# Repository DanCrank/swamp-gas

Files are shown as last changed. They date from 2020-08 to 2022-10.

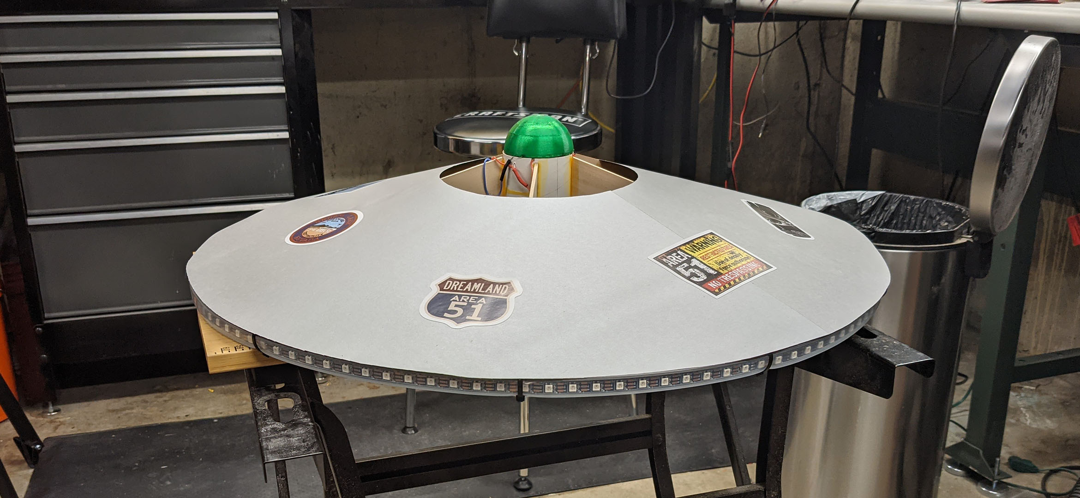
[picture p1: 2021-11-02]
swamp-gas-in-workshop.jpg

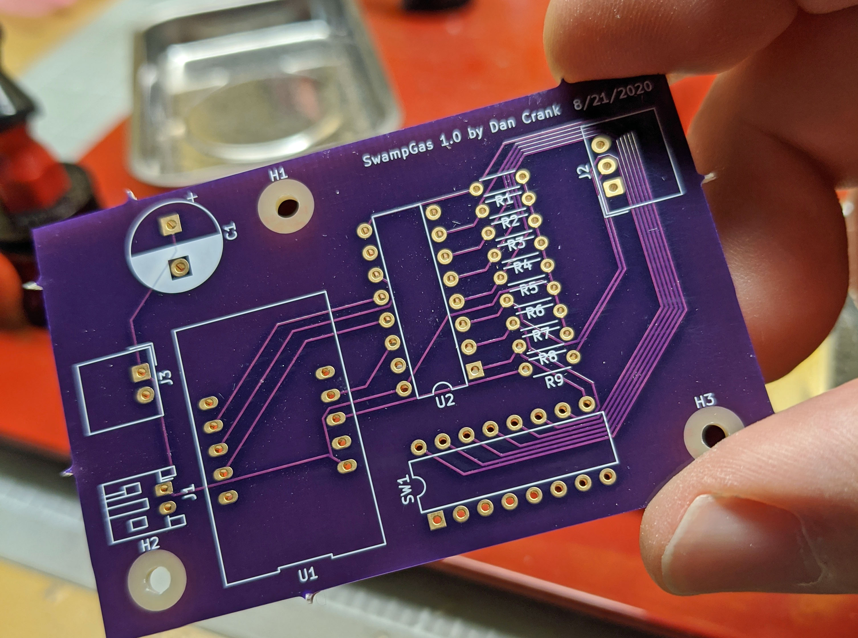
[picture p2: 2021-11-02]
lighting-controller/board/images/pcb-1.jpg

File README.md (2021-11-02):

# swamp-gas
Design for an illuminated saucer rocket

```
/3d-objects              STL files for 3D-printed parts
                         F3D and STEP files for complete rocket
/lighting-controller
  /arduino/swamp-gas     Arduino code for the lighting program
  /board                 design files for carrier PCB
    /images              images of the layout and manufactured board
```

Parts list:
- 29mm motor tube, 100mm long
- 2.6" body tube, 100mm long
- 29mm motor retainer
- 5 fins cut from 1/8" basswood, per template
- 2-meter Adafruit NeoPixel strand, 60 pixels/meter
- Adafruit Trinket M0
- Custom carrier PCB
- 4 green LEDs mounted in top of body tube to illuminate the dome
    (wired in parallel, with a current limiting resistor if needed)
- 400mAh LiPo battery (zip tied to one of the fins)
- 26 ga stranded wire
- 2-pin JST connectors for battery
- 3-pin Molex connectors for connection to NeoPixel strand
- 2-pin Molex connectors for connection to LEDs in dome
- Power switch (optional)

LED wiring is left as an exercise for the reader and will depend on
the specific LEDs and battery you use.

In the first flight, the saucer flipped nose-down at apogee and fell
in a stable nose-down orientation, so no parachute should be needed.
The nose cone can be permanently mounted in the motor tube with CA.
Make sure the ejection sharge is removed from the motor before flight.

First flight was at the St. Louis Rocketry Association Spooktacular
Night Launch on October 30, 2021.

https://youtu.be/KtkhaTuiWWw

Hardware and software designs in this repository are distributed under
GNU GPLv3. (See COPYING for full license.)

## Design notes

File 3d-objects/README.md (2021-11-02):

The nose cone was printed in translucent green PETG; the other parts
were printed in PLA.

The rocket was designed in Autodesk Fusion 360 (hobbyist version);
the full design of the rocket is provided in Fusion 360 format (.f3d)
and as a .step file.

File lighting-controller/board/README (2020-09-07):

Board designed with KiCad 5.1.6. https://www.kicad-pcb.org

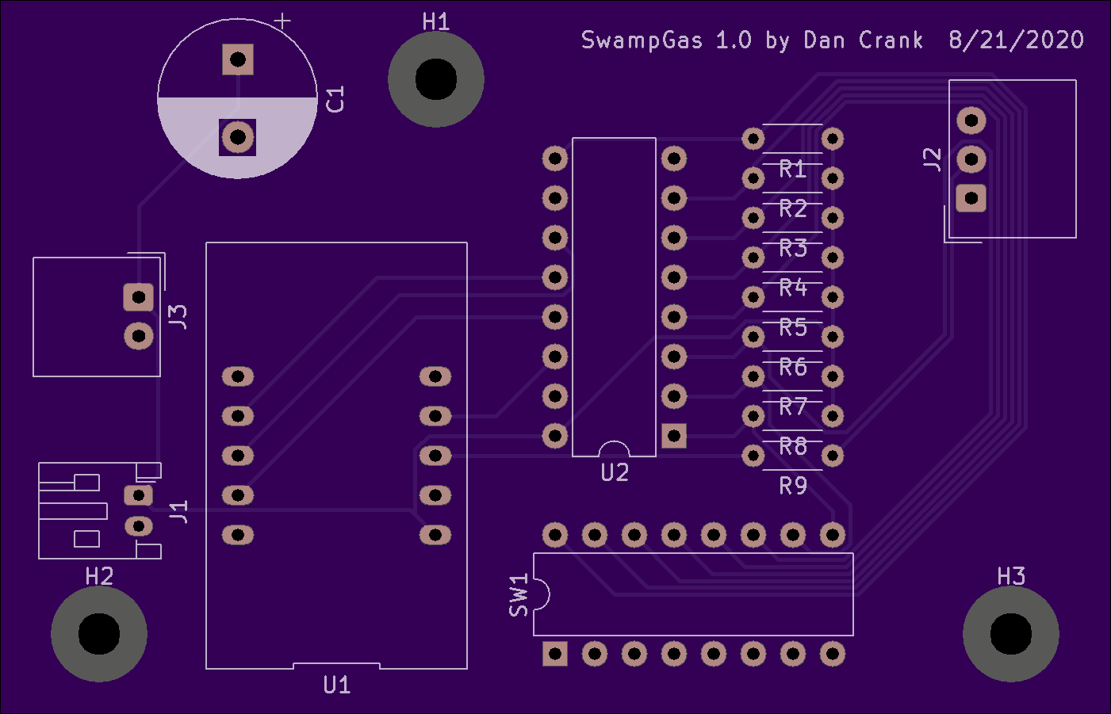
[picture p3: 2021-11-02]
lighting-controller/board/images/fab-1.0.png

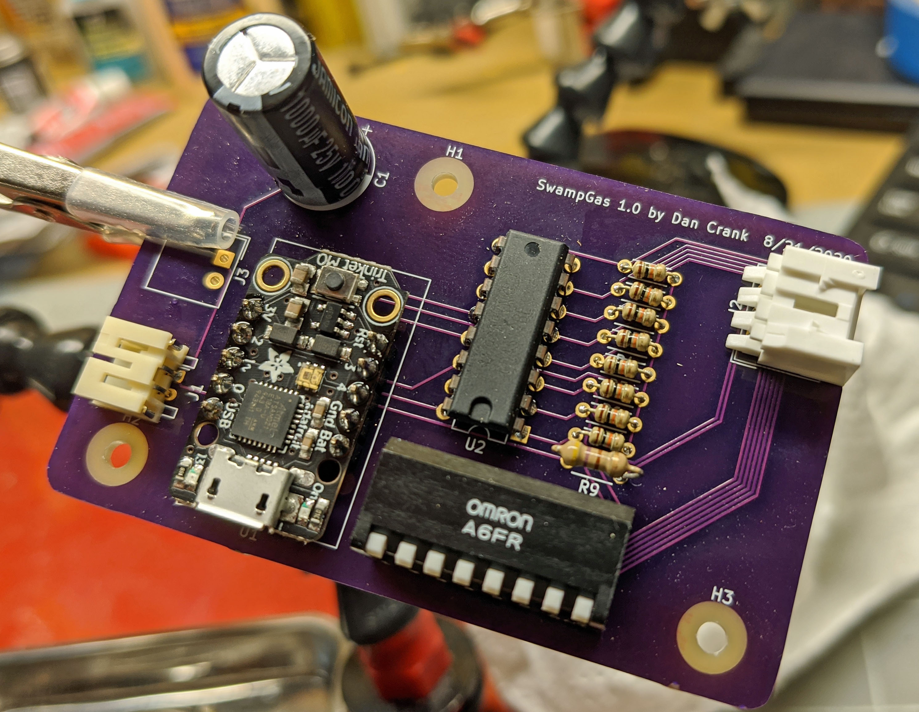
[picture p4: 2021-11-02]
lighting-controller/board/images/pcb-2.jpg

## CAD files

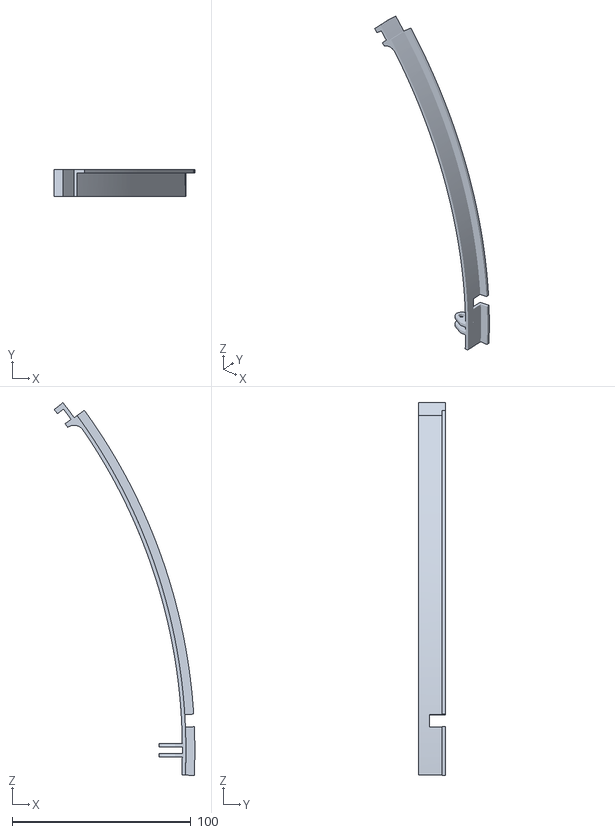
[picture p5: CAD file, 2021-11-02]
3d-objects/ring-b-with-slot.stl
78.6 x 15.0 x 208.5

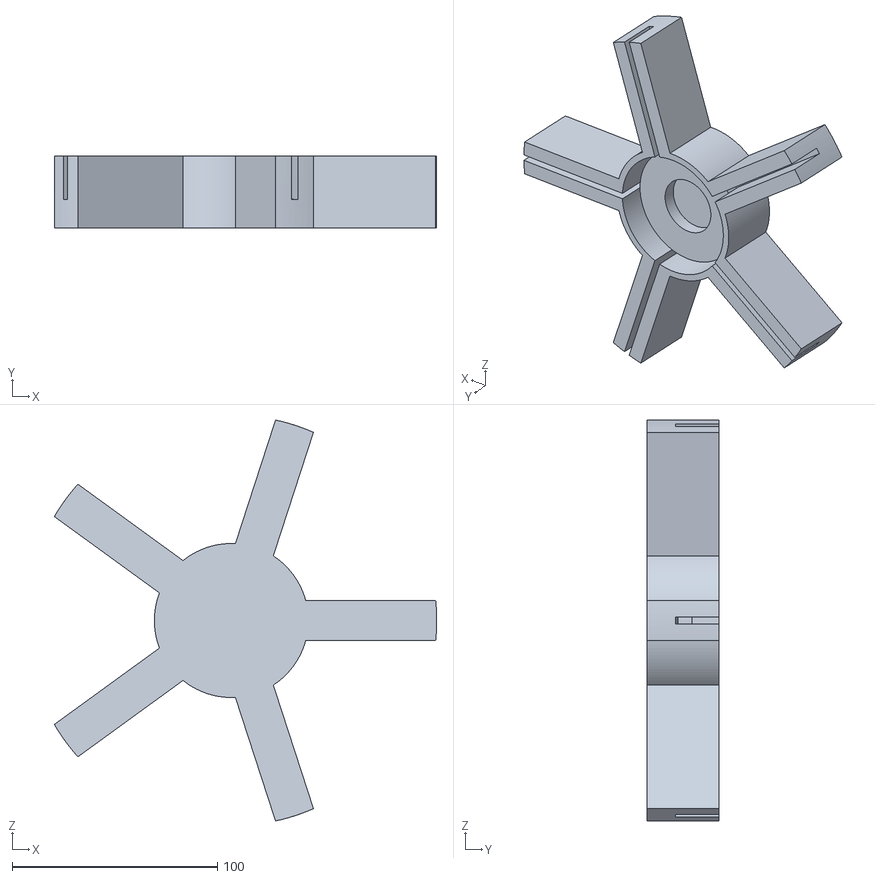
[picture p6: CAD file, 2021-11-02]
3d-objects/FinJig.stl
186.2 x 35.0 x 195.3

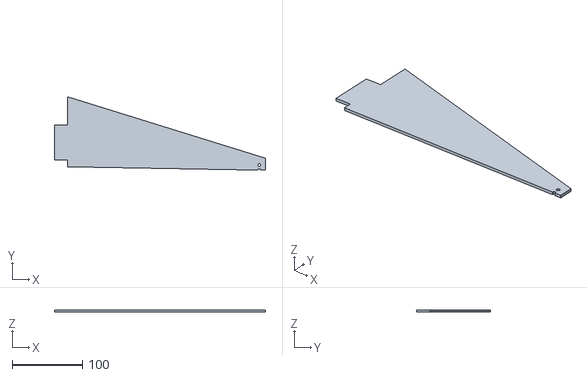
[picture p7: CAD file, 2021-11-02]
3d-objects/fin-template.stl
301.2 x 104.9 x 3.11

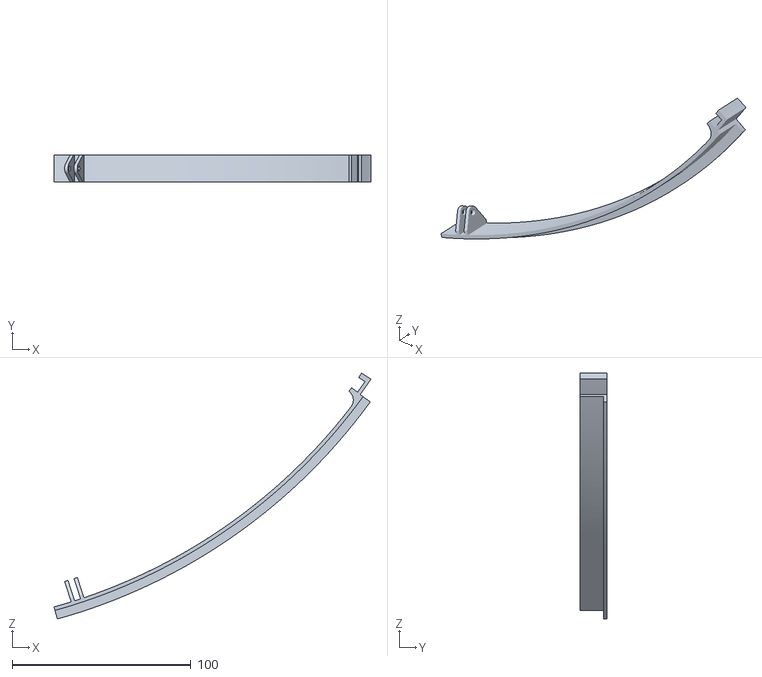
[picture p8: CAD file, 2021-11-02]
3d-objects/ring-b.stl
177.4 x 15.0 x 137.7

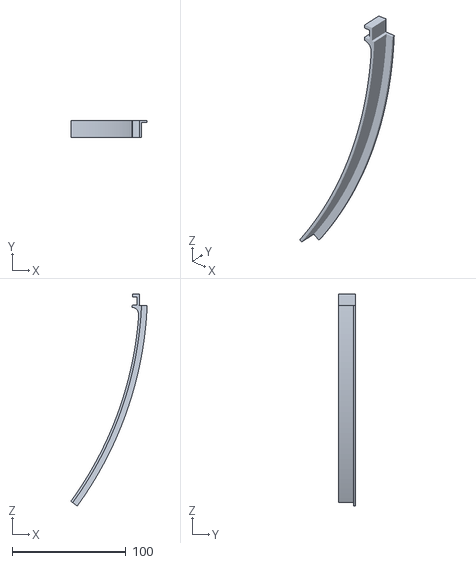
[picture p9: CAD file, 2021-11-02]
3d-objects/ring-a.stl
67.1 x 15.0 x 186.2

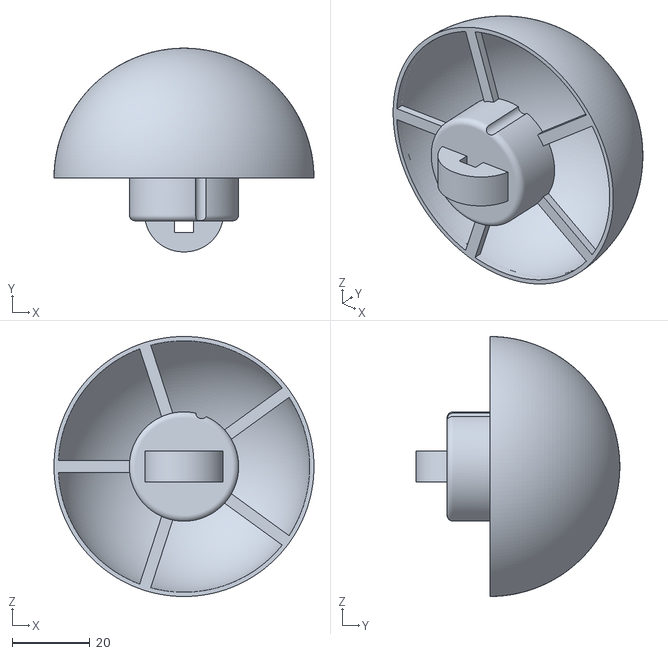
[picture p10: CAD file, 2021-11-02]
3d-objects/nose-cone-2.stl
67.1 x 52.5 x 67.1

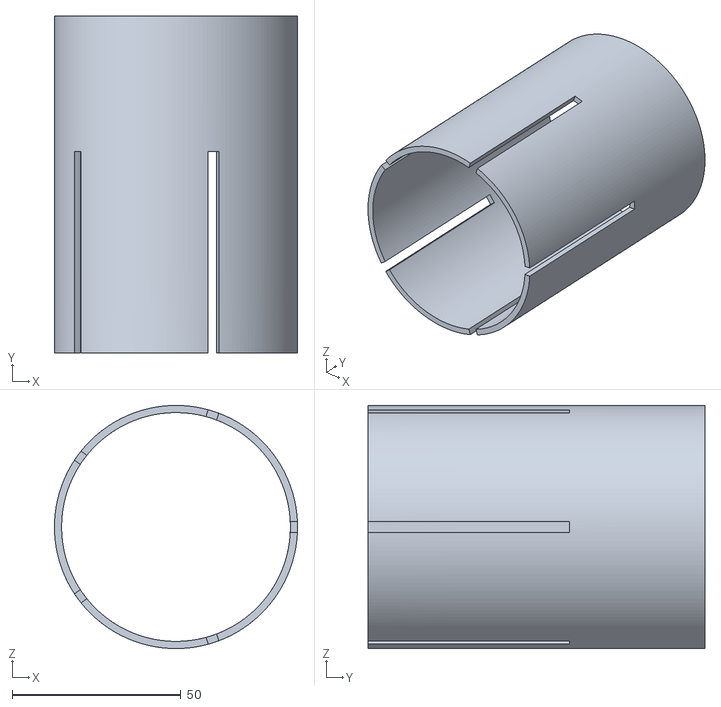
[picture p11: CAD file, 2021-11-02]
3d-objects/SlottingJig.stl
72.0 x 99.8 x 72.0

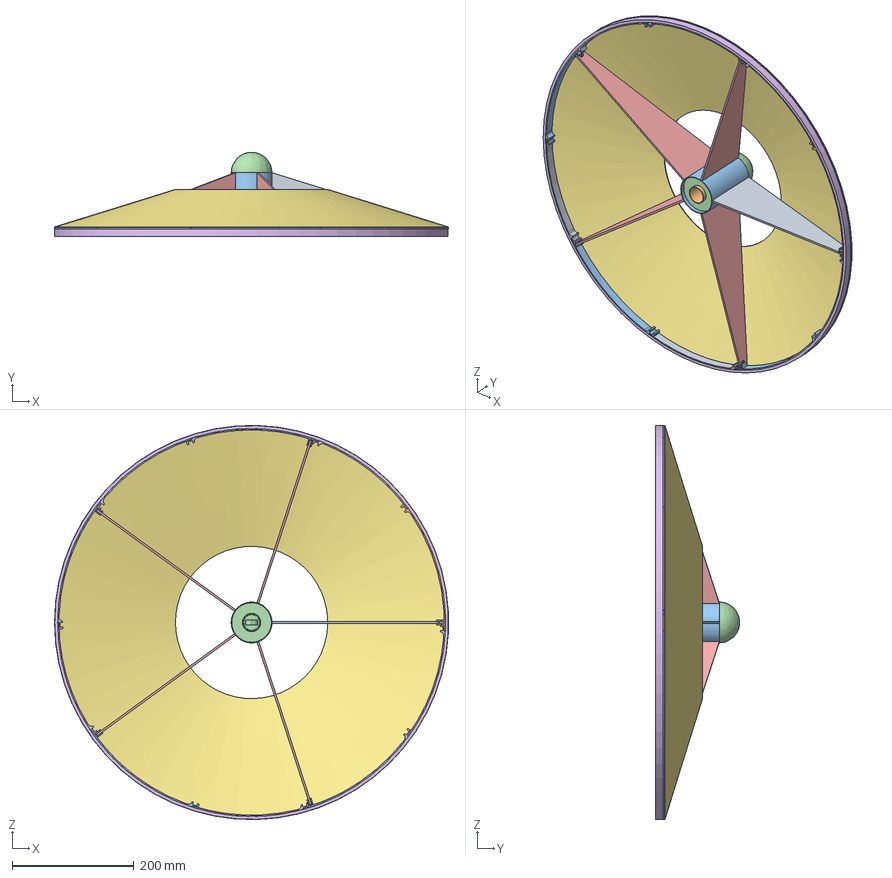
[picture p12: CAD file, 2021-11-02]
3d-objects/SwampGas.step
646.9 x 138.5 x 647.0 mm

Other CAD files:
3d-objects/SwampGas.f3d

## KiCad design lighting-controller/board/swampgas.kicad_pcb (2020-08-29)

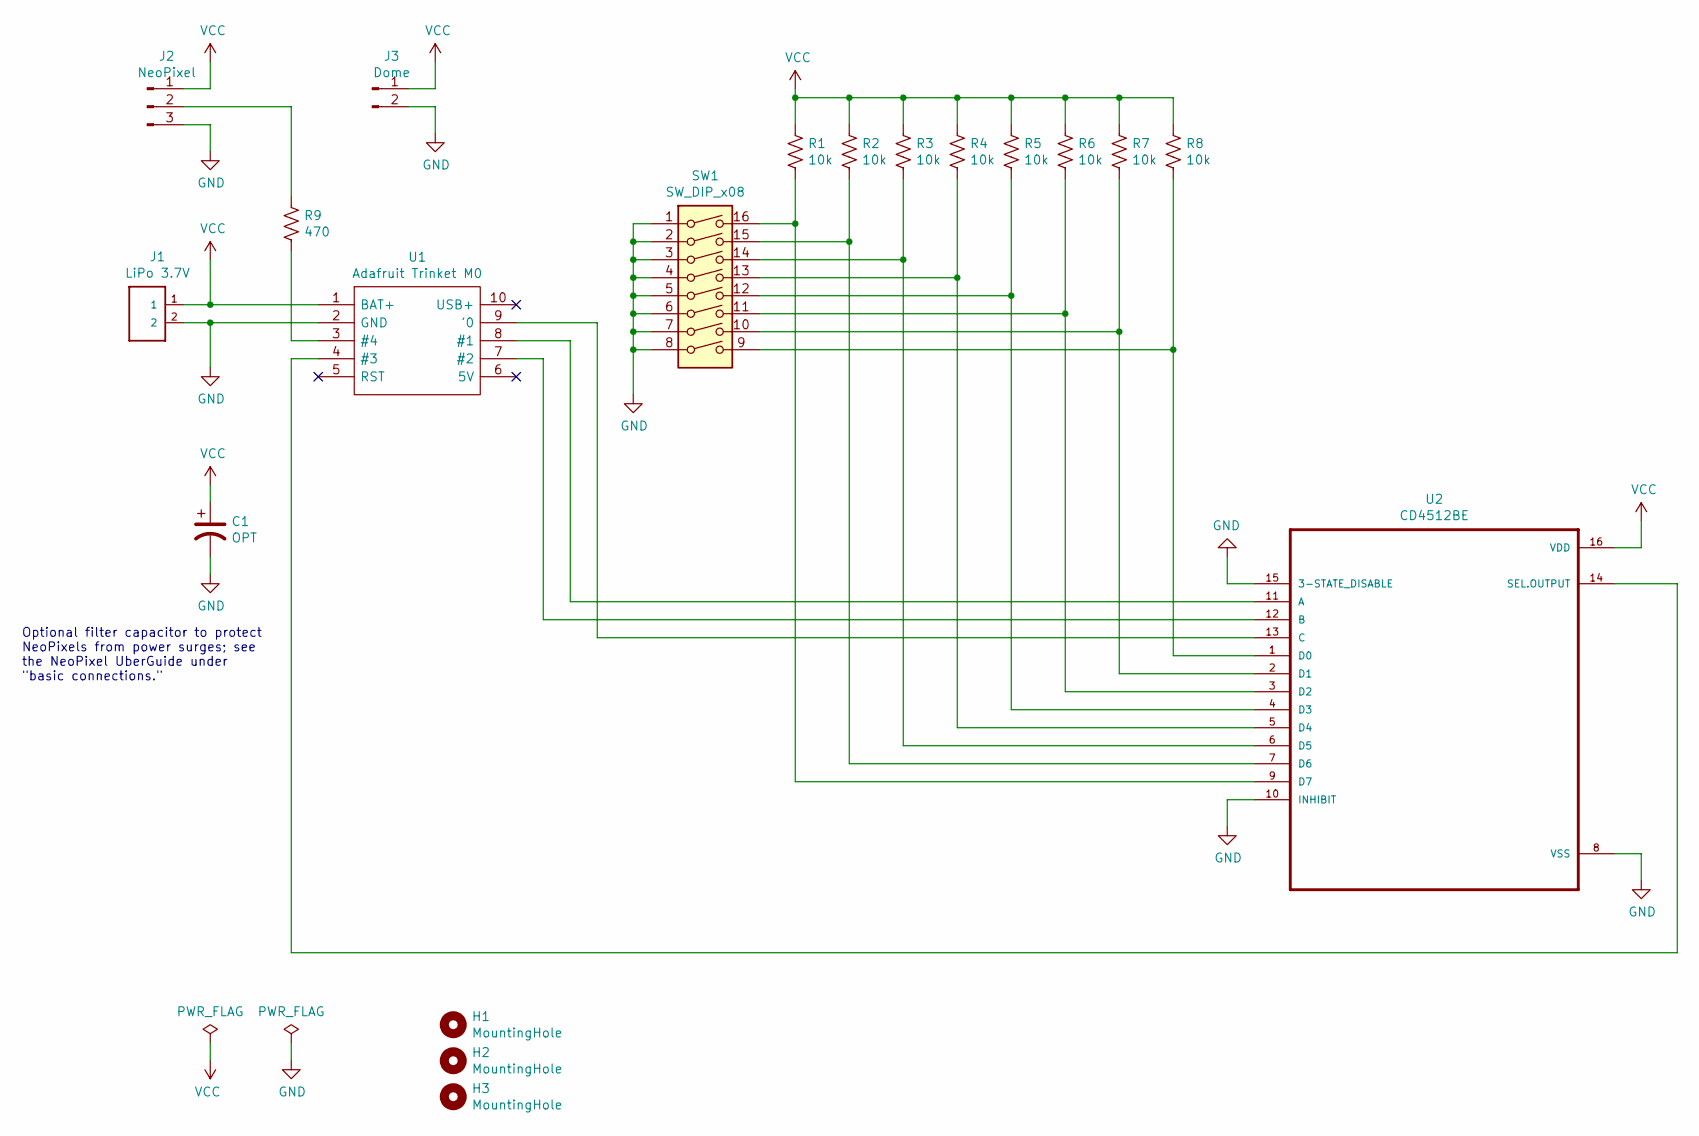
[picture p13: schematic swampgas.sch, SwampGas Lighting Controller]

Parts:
C1: OPT; CP_Radial_D10.0mm_P5.00mm
H1, H2, H3: MountingHole; MountingHole_2.7mm_M2.5
J1: LiPo 3.7V; JST_PH_S2B-PH-K_1x02_P2.00mm_Horizontal
J2: NeoPixel; Molex_SPOX_5268-03A_1x03_P2.50mm_Horizontal
J3: Dome; Molex_SPOX_5268-02A_1x02_P2.50mm_Horizontal
R1, R2, R3, R4, R5, R6, R7, R8: 10k; R_Axial_DIN0204_L3.6mm_D1.6mm_P5.08mm_Horizontal
R9: 470; R_Axial_DIN0204_L3.6mm_D1.6mm_P5.08mm_Horizontal
SW1: SW_DIP_x08; DIP-16_W7.62mm
U1: Adafruit Trinket M0; ADAFRUIT_TRINKET_M0; Manufacturer_Part_Number 3500
U2: CD4512BE; DIP-16_W7.62mm

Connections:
GND: C1.2, J1.2, J2.3, J3.2, SW1.1, SW1.2, SW1.3, SW1.4, SW1.5, SW1.6, SW1.7, SW1.8, U1.2 (GND), U2.8 (VSS), U2.10 (INHIBIT), U2.15 (3-STATE_DISABLE)
unnamed: J2.2, R9.1
unnamed: R1.2, SW1.16, U2.9 (D7)
unnamed: R2.2, SW1.15, U2.7 (D6)
unnamed: R3.2, SW1.14, U2.6 (D5)
unnamed: R4.2, SW1.13, U2.5 (D4)
unnamed: R5.2, SW1.12, U2.4 (D3)
unnamed: R6.2, SW1.11, U2.3 (D2)
unnamed: R7.2, SW1.10, U2.2 (D1)
unnamed: R8.2, SW1.9, U2.1 (D0)
unnamed: R9.2, U1.3 (#4)
unnamed: U1.4 (#3), U2.14 (SEL.OUTPUT)
unnamed: U1.7 (#2), U2.12 (B)
unnamed: U1.8 (#1), U2.11 (A)
unnamed: U1.9 ('0), U2.13 (C)
VCC: C1.1, J1.1, J2.1, J3.1, R1.1, R2.1, R3.1, R4.1, R5.1, R6.1, R7.1, R8.1, U1.1 (BAT+), U2.16 (VDD)

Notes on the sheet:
Optional filter capacitor to protect NeoPixels from power surges; see the NeoPixel UberGuide under "basic connections."

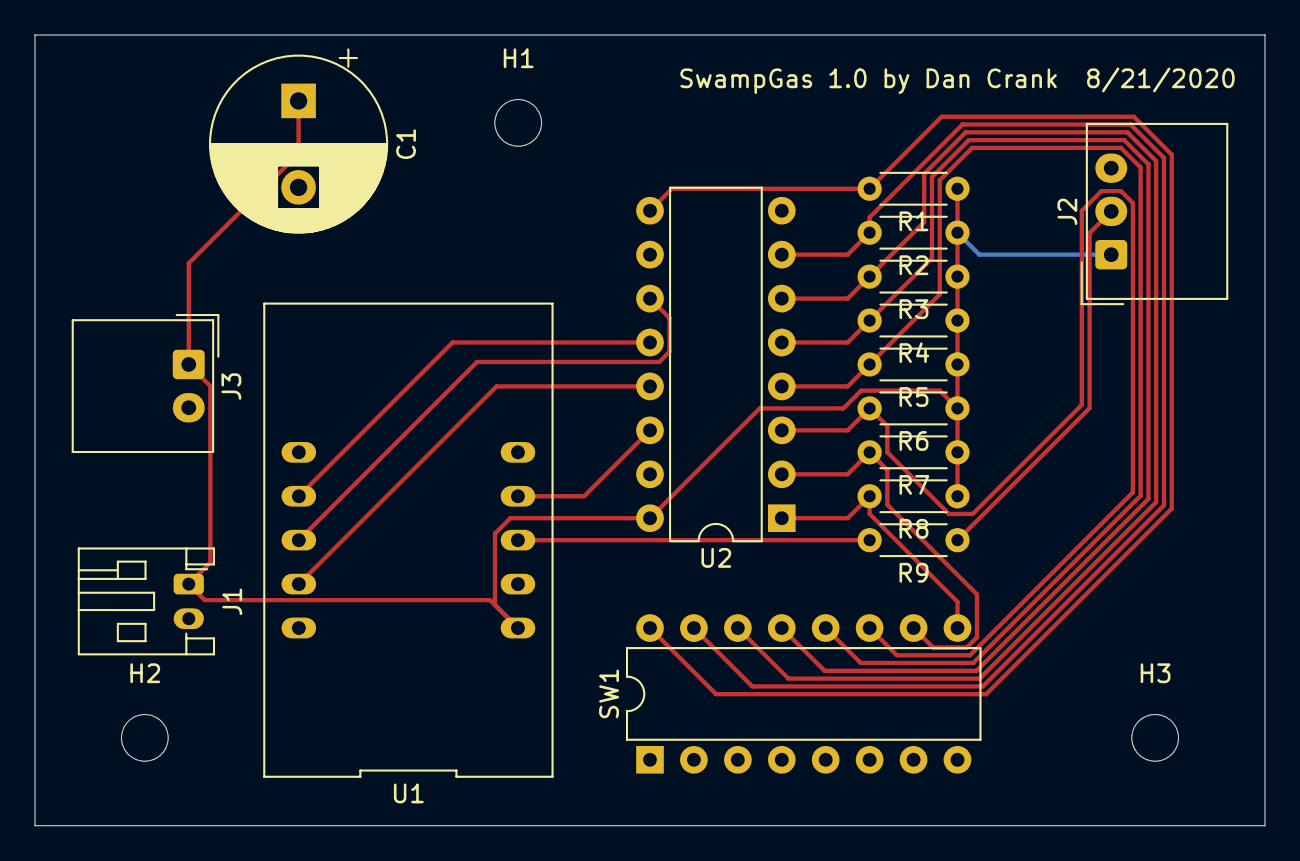
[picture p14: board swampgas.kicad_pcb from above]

Board: 2 copper layers, 71.1 x 45.7 mm, 19 parts (0 on the bottom side), 16 nets.

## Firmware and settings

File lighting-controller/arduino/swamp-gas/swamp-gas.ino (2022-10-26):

/*
 * swamp-gas.ino: lighting controller code for a flying saucer, based on Arduino & NeoPixel.
 * Copyright (C) 2020 Dan Crank (danno@danno.org)
 *
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
 * You should have received a copy of the GNU General Public License
 * along with this program.  If not, see <https://www.gnu.org/licenses/>.
 */

#include <Adafruit_NeoPixel.h>
#ifdef __AVR__
  #include <avr/power.h>
#endif

#define NUM_PIXELS 120
#define PIXEL_PIN 4
#define PIXEL_BRIGHTNESS_HIGH 255 // scale of 255
#define PIXEL_BRIGHTNESS_LOW 128 // scale of 255

// multiplexer A (LSB) to trinket A0 (Arduino pin 1!) as digital out
#define MUX0_PIN 1
// multiplexer B       to trinket A1 (Arduino pin 2!) as digital out
#define MUX1_PIN 2
// multiplexer C (MSB) to trinket A2 (Arduino pin 0!) as digital out
#define MUX2_PIN 0
// multiplexer out     to trinket A3 (pin labeled 3) as digital in
#define MUXOUT_PIN 3

Adafruit_NeoPixel strip;

void setup() {
  Serial.println("SwampGas 1.1 Copyright (C) 2021 Dan Crank (danno@danno.org)");
  Serial.println("This program comes with ABSOLUTELY NO WARRANTY.");
  randomSeed(analogRead(0));
  strip = Adafruit_NeoPixel(NUM_PIXELS, PIXEL_PIN, NEO_GRB + NEO_KHZ800);
  strip.begin();
  int iDipswitch = readDipswitch();
  int fBrightness = (iDipswitch & 0x01); //bit 0
  if (fBrightness)
    strip.setBrightness(PIXEL_BRIGHTNESS_HIGH);
  else
    strip.setBrightness(PIXEL_BRIGHTNESS_LOW);
  strip.clear(); // Initialize all pixels to 'off'
  strip.show();
  pinMode(MUX0_PIN, OUTPUT);
  pinMode(MUX1_PIN, OUTPUT);
  pinMode(MUX2_PIN, OUTPUT);
  pinMode(MUXOUT_PIN, INPUT); //circuit has pull-ups on the input side of the mux
}

void loop() {
  int iDipswitch = readDipswitch();
  int iPattern = (iDipswitch >> 5 & 0x07); //bits 7-5
  int iColorIndex = (iDipswitch >> 1 & 0x0F); //bits 4-1
  switch (iPattern) {
    case 0:
      //clockwise sweep fast
      counterClockwiseSweep(iColorIndex, 24, 1);
      break;
    case 1:
      //clockwise sweep slow
      counterClockwiseSweep(iColorIndex, 24, 15);
      break;
    case 2:
      //3-way bounce
      bounce(iColorIndex, 10, 3, 20);
      break;
    case 3:
      //6-way bounce
      bounce(iColorIndex, 10, 6, 30);
      break;
    case 4:
      //pulse fast
      pulse(iColorIndex, 3);
      break;
    case 5:
      //pulse slow
      pulse(iColorIndex, 1);
      break;
    case 6:
      dropout(iColorIndex, 1, 20);
      break;
    case 7:
      //everything bagel (2022)
      strip.fill(strip.Color(0,0,0));
      strip.show();
      for (int q = 0; q < 5; q++) {
        counterClockwiseSweepIncreasingSpeed(iColorIndex, 36);
        counterClockwiseSweepDecreasingSpeed(iColorIndex, 36);
      }
      strip.fill(strip.Color(0,0,0));
      strip.show();
      for (int q = 0; q < 2; q++) {
        for (int w = 1; w < 21; w++) {
          pulse(iColorIndex, w);
        }
        for (int w = 20; w > 0; w--) {
          pulse(iColorIndex, w);
        }
      }
      strip.fill(strip.Color(0,0,0));
      strip.show();
      for (int q = 0; q < 6; q++) {
        dropout(iColorIndex, 1, 5);
      }
      strip.fill(strip.Color(0,0,0));
      strip.show();
      //everything bagel (2021)
      //for (int q = 0; q < 3; q++) {
      //  clockwiseSweep(iColorIndex, 24, 1);
      //}
      //strip.fill(strip.Color(0,0,0));
      //strip.show();
      //for (int q = 0; q < 3; q++) {
      //  counterClockwiseSweep(iColorIndex, 24, 1);
      //}
      //strip.fill(strip.Color(0,0,0));
      //strip.show();
      //for (int w = 1; w < 21; w++) {
      //  pulse(iColorIndex, w);
      //}
      //for (int q = 0; q < 3; q++) {
      //  dropout(iColorIndex, 1, 20);
      //}
      break;
    default: //should never happen
      delay(200);
  }
}

// swampgas color constants (indexed to dip switch selections)
#define WHITE 0
#define RED 1
#define BLUE 2
#define GREEN 3
#define YELLOW 4
#define CYAN 5
#define PURPLE 6
// 7-13 TBD; will return white
#define RAINBOW_FAST 14
#define RAINBOW_SLOW 15

// color mapping
uint32_t mapColor(int iColorIndex) {
  switch (iColorIndex) {
    case WHITE: return strip.Color(255, 255, 255);
    case RED: return strip.Color(255, 0, 0);
    case BLUE: return strip.Color(0, 0, 255);
    case GREEN: return strip.Color(0, 255, 0);
    case YELLOW: return strip.Color(255, 150, 0);
    case CYAN: return strip.Color(0, 255, 255);
    case PURPLE: return strip.Color(180, 0, 255);
    case RAINBOW_SLOW: return rainbow(10.0);
    case RAINBOW_FAST: return rainbow(20.0);
    default: return strip.Color(255, 255, 255);
  }
}

// returns true if the index refers to a changing color (such as rainbow);
// animation functions can call this to determine whether they need to
// update the color during animations.
boolean isDynamicColor(int iColorIndex) {
  switch (iColorIndex) {
    case RAINBOW_SLOW:
    case RAINBOW_FAST:
      return true;
    default: return false;
  }
}

uint32_t rainbow(double dCyclesPerMinute) {
  // return a rainbow color based on the millis() value
  int i = ((int)(((double)(millis()) * 256.0 / (60000.0 / dCyclesPerMinute)))) % 256;
  // the lines below are adapted from the Adafruit NeoPixel demo code
  // https://github.com/adafruit/Adafruit_CircuitPython_NeoPixel (MIT license)
  // The colours are a transition r - g - b - back to r.
  if ((i < 0) || (i > 255))
    return strip.Color(0, 0, 0);
  if (i < 85)
    return strip.Color(255 - i * 3, i * 3, 0);
  if (i < 170)
  {
    i -= 85;
    return strip.Color(0, 255 - i * 3, i * 3);
  }
  i -= 170;
  return strip.Color(i * 3, 0, 255 - i * 3);
}

uint32_t fade(uint32_t color, double frac) {
  if (frac == 0.0) return strip.Color(0, 0, 0);
  int red = color >> 16 & 0xFF;
  int green = color >> 8 & 0xFF;
  int blue = color & 0xFF;
  return strip.Color(int(red * frac * frac),
                     int(green * frac * frac),
                     int(blue * frac * frac));
}

int bounceRight(int iPos, int iPixelsPerSide) {
  if (iPos >= iPixelsPerSide)
    return (iPixelsPerSide - (iPos - iPixelsPerSide) - 2);
  return iPos;
}

int bounceLeft(int iPos) {
  if (iPos < 0)
    return (iPos * -1);
  return iPos;
}

void clockwiseSweep(int iColorIndex, int iWidth, int iWait) {
  uint32_t color = mapColor(iColorIndex);
  for (int i = NUM_PIXELS-1; i >= 0; i--) {
    if (isDynamicColor(iColorIndex)) color = mapColor(iColorIndex);
    for (int j = 0; j <= iWidth; j++)
      strip.setPixelColor(((i - j) % NUM_PIXELS), fade(color, ((double)j / (double)iWidth)));
    strip.show();
    if (iWait > 0) delay(iWait);
  }
}

void counterClockwiseSweep(int iColorIndex, int iWidth, int iWait) {
  uint32_t color = mapColor(iColorIndex);
  for (int i = 0; i < NUM_PIXELS; i++) {
    if (isDynamicColor(iColorIndex)) color = mapColor(iColorIndex);
    for (int j = 0; j <= iWidth; j++)
      strip.setPixelColor(((i + j) % NUM_PIXELS), fade(color, ((double)j / (double)iWidth)));
    strip.show();
    if (iWait > 0) delay(iWait);
  }
}

void counterClockwiseSweepIncreasingSpeed(int iColorIndex, int iWidth) {
  uint32_t color = mapColor(iColorIndex);
  for (int iWait = 3; iWait >= 0; iWait--) {
    for (int i = 0; i < NUM_PIXELS; i++) {
      if (isDynamicColor(iColorIndex)) color = mapColor(iColorIndex);
      for (int j = 0; j <= iWidth; j++)
        strip.setPixelColor(((i + j) % NUM_PIXELS), fade(color, ((double)j / (double)iWidth)));
      strip.show();
      if (iWait > 0) delay(iWait * 2);
    }
  }
}

void counterClockwiseSweepDecreasingSpeed(int iColorIndex, int iWidth) {
  uint32_t color = mapColor(iColorIndex);
  for (int iWait = 0; iWait >= 3; iWait++) {
    for (int i = 0; i < NUM_PIXELS; i++) {
      if (isDynamicColor(iColorIndex)) color = mapColor(iColorIndex);
      for (int j = 0; j <= iWidth; j++)
        strip.setPixelColor(((i + j) % NUM_PIXELS), fade(color, ((double)j / (double)iWidth)));
      strip.show();
      if (iWait > 0) delay(iWait * 2);
    }
  }
}

void bounce(int iColorIndex, int iWidth, int iSides, int iWait) {
  int iPixelsPerSide = int(NUM_PIXELS / iSides);
  uint32_t color = mapColor(iColorIndex);
  for (int i = 0; i < iPixelsPerSide; i++) {
    // sweeping left to right
    if (isDynamicColor(iColorIndex)) color = mapColor(iColorIndex);
    for (int j = 0; j < (iWidth + 1); j++)
      for (int k = 0; k < NUM_PIXELS; k += iPixelsPerSide)
        strip.setPixelColor(bounceRight(i + j, iPixelsPerSide) + k, fade(color, ((double)j / (double)iWidth)));
    strip.show();
    if (iWait > 0) delay(iWait);
  }
  for (int i = iPixelsPerSide - 2; i > 1; i -= 1) {
    // sweeping right to left
    if (isDynamicColor(iColorIndex)) color = mapColor(iColorIndex);
    for (int j = 0; j <= iWidth; j++)
      for (int k = 0; k < NUM_PIXELS; k += iPixelsPerSide)
        strip.setPixelColor(bounceLeft(i - j) + k, fade(color, ((double)j / (double)iWidth)));
    strip.show();
    if (iWait > 0) delay(iWait);
  }
}

void pulse(int iColorIndex, int iSpeed) {
  uint32_t color = mapColor(iColorIndex);
  strip.clear();
  strip.show();
  for (int i = 0; i <= 100; i += iSpeed) {
    if (isDynamicColor(iColorIndex)) color = mapColor(iColorIndex);
    strip.fill(fade(color, (double)(i) / 100.0));
    strip.show();
  }
  for (int i = 100; i >= 0; i -= iSpeed) {
    if (isDynamicColor(iColorIndex)) color = mapColor(iColorIndex);
    strip.fill(fade(color, (double)(i) / 100.0));
    strip.show();
  }
}

void dropout(int iColorIndex, int iFadeupSpeed, int iDropoutWait) {
  uint32_t color = mapColor(iColorIndex);
  strip.clear();
  strip.show();
  // fade up
  for (int i = 0; i <= 100; i += iFadeupSpeed) {
    if (isDynamicColor(iColorIndex)) color = mapColor(iColorIndex);
    strip.fill(fade(color, (double)(i) / 100.0));
    strip.show();
  }
  for (int w = 0; w < NUM_PIXELS; w++) {
    // randomly drop pixels one at a time
    // pick a pixel
    int iPixel = (int)(random(NUM_PIXELS));
    if (strip.getPixelColor(iPixel) != 0) {
      // if it's on, turn it off
      strip.setPixelColor(iPixel, strip.Color(255, 255, 255));
      strip.show();
      delay(7);
      strip.setPixelColor(iPixel, strip.Color(0, 0, 0));
    } else {
      // otherwise, find the next pixel that's on turn that one off
      for (int j = 1; j < NUM_PIXELS; j++) {
        if (strip.getPixelColor(iPixel + j % NUM_PIXELS) != 0) {
          strip.setPixelColor(iPixel + j % NUM_PIXELS, strip.Color(255, 255, 255));
          strip.show();
          delay(7);
          strip.setPixelColor(iPixel + j % NUM_PIXELS, strip.Color(0, 0, 0));
          break;
        }
      }
    }
    strip.show();
    if (iDropoutWait > 0) delay(iDropoutWait);
  }
}

int readDipswitchPin(int iPin) {
  if ((iPin < 0) || (iPin > 7)) { Serial.println("WARN: dipswitch pin index out of range"); return false; }
  // address the mux
  if (iPin & 0x4) digitalWrite(MUX2_PIN, HIGH); else digitalWrite(MUX2_PIN, LOW); //really?
  if (iPin & 0x2) digitalWrite(MUX1_PIN, HIGH); else digitalWrite(MUX1_PIN, LOW);
  if (iPin & 0x1) digitalWrite(MUX0_PIN, HIGH); else digitalWrite(MUX0_PIN, LOW);
  // settle
  delay(1);
  //read the mux output (NOTE: active LOW)
  if (digitalRead(MUXOUT_PIN) == LOW) return 1; else return 0; //REALLY really?
}

int readDipswitch() {
  int iValue = 0;
  for (int i = 0; i < 8; i++) {
    int iPinVal = readDipswitchPin(i);
    iValue += iPinVal << i;
  }
  return iValue;
}

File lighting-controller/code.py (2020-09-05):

# SwampGas 1.0
# based on "CircuitPython demo - NeoPixel" by AdaFruit

# NOTE: current breadboard prototype is wired with the
# dip switch LSB on the left (position 1). probably
# want to reverse that on the real one.

import time
import board
import neopixel
from digitalio import DigitalInOut, Direction

print("SwampGas 1.0 startup")
# multiplexer A (LSB) to trinket A0 (pin labeled 1!) as digital out
mux_0 = DigitalInOut(board.A0)
mux_0.direction = Direction.OUTPUT
# multiplexer B       to trinket A1 (pin labeled 2!) as digital out
mux_1 = DigitalInOut(board.A1)
mux_1.direction = Direction.OUTPUT
# multiplexer C (MSB) to trinket A2 (pin labeled 0!) as digital out
mux_2 = DigitalInOut(board.A2)
mux_2.direction = Direction.OUTPUT
# multiplexer out     to trinket A3 (pin labeled 3) as digital in
mux_out = DigitalInOut(board.A3)
mux_out.direction = Direction.INPUT
mux_out.pull = None  # circuit has pull-ups on the input side of the mux
# neopixel data-in    to trinket A4 (pin labeled 4) as bare pin
# (neopixel driver knows what to do with it)
pixel_pin = board.A4
# using 60 NeoPixels on 1m strip
num_pixels = 60
# current draw is roughly proportional to brightness but also
# depends a great deal on the lighting pattern.
neopixel_brightness = 1.0


pixels = neopixel.NeoPixel(pixel_pin,
                           num_pixels,
                           brightness=neopixel_brightness,
                           auto_write=False)


# never apologize, never explain
rainbow_magic = 0
rainbow_speed = 16


def taste_the_rainbow():
    global rainbow_magic
    rainbow_magic = (rainbow_magic + rainbow_speed) % 256


# swampgas color constants (indexed to dip switch selections)
WHITE = 0
RED = 1
BLUE = 2
GREEN = 3
YELLOW = 4
CYAN = 5
PURPLE = 6
# 7-14 TBD; will return black
RAINBOW = 15


# color mapping
def color(select):
    if select == WHITE: return (255, 255, 255)
    elif select == RED: return (255, 0, 0)
    elif select == BLUE: return (0, 0, 255)
    elif select == GREEN: return (0, 255, 0)
    elif select == YELLOW: return (255, 150, 0)
    elif select == CYAN: return (0, 255, 255)
    elif select == PURPLE: return (180, 0, 255)
    elif select == RAINBOW: return wheel(rainbow_magic)
    else: return (0, 0, 0)


def wheel(pos):
    # Input a value 0 to 255 to get a color value.
    # The colours are a transition r - g - b - back to r.
    if pos < 0 or pos > 255:
        return (0, 0, 0)
    if pos < 85:
        return (255 - pos * 3, pos * 3, 0)
    if pos < 170:
        pos -= 85
        return (0, 255 - pos * 3, pos * 3)
    pos -= 170
    return (pos * 3, 0, 255 - pos * 3)


def fade(color, frac):
    if frac == 0:
        return (0, 0, 0)
    return(int(color[0] * frac * frac),
           int(color[1] * frac * frac),
           int(color[2] * frac * frac))


def bounce_right(pos, pixels_per_side):
    if pos >= pixels_per_side:
        return pixels_per_side - (pos - pixels_per_side) - 2
    return pos


def bounce_left(pos):
    if pos < 0:
        return pos * -1
    return pos


def clockwise_sweep(color, width, wait):
    for i in range(num_pixels):
        for j in range(width + 1):
            pixels[(i + j) % num_pixels] = fade(color, (j / width))
        pixels.show()
        if wait > 0: time.sleep(wait)


def bounce(color, width, sides, wait):
    pixels_per_side = int(num_pixels / sides)
    for i in range(pixels_per_side):
        # sweeping left to right
        for j in range(width + 1):
            for k in range(0, num_pixels, pixels_per_side):
                pixels[bounce_right(i + j, pixels_per_side) + k] = \
                    fade(color, (j / width))
        pixels.show()
        if wait > 0: time.sleep(wait)
    for i in range(pixels_per_side - 2, 1, -1):
        # sweeping right to left
        for j in range(width + 1):
            for k in range(0, num_pixels, pixels_per_side):
                pixels[bounce_left(i - j) + k] = fade(color, (j / width))
        pixels.show()
        if wait > 0: time.sleep(wait)


def read_dipswitch_pin(pin):
    if pin < 0 or pin > 7:
        raise IndexError
    # address the mux
    mux_2.value = pin >> 2 & 1
    mux_1.value = pin >> 1 & 1
    mux_0.value = pin & 1
    # settle
    # time.sleep(0.02)
    # read the mux output (NOTE: active LOW)
    return not mux_out.value


def read_dipswitch():
    dip_value = 0
    for i in range(8):
        dip_value += read_dipswitch_pin(i) << i
    return dip_value


# main loop
# TODO: turn off built-in neopixel
while True:
    pixels.fill((0, 0, 0))
    pixels.show()
    # which color and pattern?
    select = read_dipswitch()
    select_color = select & 0x0F
    select_pattern = select >> 4
    if select_pattern == 0:
        # 0 = clockwise sweep fast
        clockwise_sweep(color(select_color), 12, 0)
    elif select_pattern == 1:
        # 1 = clockwise sweep slow
        clockwise_sweep(color(select_color), 12, 0.05)
    elif select_pattern == 2:
        # 2 = 3-way bounce
        bounce(color(select_color), 3, 3, 0)
    elif select_pattern == 3:
        # 3 = 6-way bounce
        bounce(color(select_color), 3, 6, 0)
    # elif select_pattern == 4:
        # 4 = 
    # elif select_pattern == 5:
        # 5 = 
    # elif select_pattern == 6:
        # 6 = 
    # elif select_pattern == 7:
        # 7 = 
    # elif select_pattern == 8:
        # 8 = 
    # elif select_pattern == 9:
        # 9 = 
    # elif select_pattern == 10:
        # 10 = 
    # elif select_pattern == 11:
        # 11 = 
    # elif select_pattern == 12:
        # 12 = 
    # elif select_pattern == 13:
        # 13 = 
    # elif select_pattern == 14:
        # 14 = 
    # elif select_pattern == 15:
        # 15 = 
    else:
        # undefined
        time.sleep(1)
    taste_the_rainbow()

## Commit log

2020-08-29 Added lighting controller
    [swampgas.kicad_pcb, swampgas.sch]
2020-09-05 Lighting controller code update
    This version of the lighting controller has a very noticable delay in
    the animation cycle while it reads the dip switch (even without the
    settle delay in the dip switch function). CircuitPython does not
    natively support any kind of threading or async. Researching this
    but might convert to native Arduino if that can handle it better.
2020-09-06 Convert from CircuitPython to Arduino
    Due to problems interleaving the dip switch read function with
    the lighting animation in CircuitPython, I rewrote this using
    the Arduino libraries - much faster! :)
    [swamp-gas.ino]
2020-09-07 Refactor dynamic color code
    Refactored to make it easier to add other dynamic colors besides
    rainbow; updated the rainbow code to use millis() to drive changes
    instead of a loop counter and allow variation of cycle speed.
2020-09-07 Added pulse pattern and GPL license
    Also bumped Arduino code down a level into an "arduino" directory
    and removed the old CircuitPython file.
2020-09-07 Added README for board.
2020-09-13 3D design for fin and fin guide
    Polished up the Fusion360 model and exported a fin template and a
    guide to hold the fins to the motor tube for assembly.
    [FinGuide.stl, FinTemplate.stl]
2021-10-30 Version 1.1 - flying Oct 30 2021!
    [FinGuide.stl, motor-tube-cut-guide.stl, swampgas.sch]
2021-11-02 Full update after first flight
    [FinGuide.stl, FinJig.stl, FinTemplate.stl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]

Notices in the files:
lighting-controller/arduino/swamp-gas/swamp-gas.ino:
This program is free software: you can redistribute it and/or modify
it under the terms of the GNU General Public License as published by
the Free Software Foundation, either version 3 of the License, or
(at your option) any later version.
